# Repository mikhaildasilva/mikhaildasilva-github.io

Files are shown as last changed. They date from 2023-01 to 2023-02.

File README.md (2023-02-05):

## Cordelia 

---

<div align="center">
swimming
</div>
<div align="center"> <b>Video 1</b>: Ocillation gait</div><br>

## Design and Fabrication

---

<div align="center">
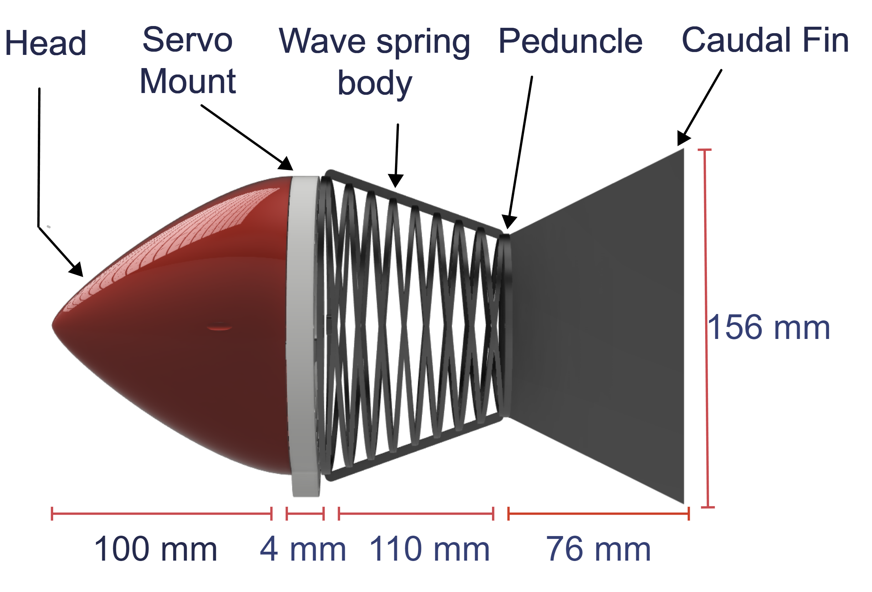
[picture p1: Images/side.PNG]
Parts

</div>

<div align="center"> <b>Figure 1</b>: Components of a single module fish </div><br>

<details open>
    <summary><b>Table 1</b>: Component and material used.</summary>
    <ol>
        <li>Component link takes you to <a href="https://gitlab.com/mikhaildasilva/fish/-/tree/main/CAD">CAD</a></li>
        <li>Material link take you to <a href="https://gitlab.com/mikhaildasilva/fish/-/tree/main/Additive%20Manufacturing/Material-Profile">Material-Profile</a></li>
    </ol>
</details>

| [Rigid head](https://gitlab.com/mikhaildasilva/fish/-/tree/main/CAD/Head)  | [Servo mount](https://gitlab.com/mikhaildasilva/fish/-/tree/main/CAD/Servo-Mount) | [Flexible body](https://gitlab.com/mikhaildasilva/fish/-/tree/main/CAD/Body) | [Caudal fin](https://gitlab.com/mikhaildasilva/fish/-/tree/main/CAD/Caudal-Fin) |
| :---: | :---: | :---: |:---: |
|[CPE](https://gitlab.com/mikhaildasilva/fish/-/tree/main/Additive%20Manufacturing/Material-Profile/CPE) | [PETG](https://gitlab.com/mikhaildasilva/fish/-/tree/main/Additive%20Manufacturing/Material-Profile/PETG) |  [TPU-95A](https://gitlab.com/mikhaildasilva/fish/-/tree/main/Additive%20Manufacturing/Material-Profile/TPU) |[TPU-95A](https://gitlab.com/mikhaildasilva/fish/-/tree/main/Additive%20Manufacturing/Material-Profile/TPU) |

---

:exclamation: A modular approach gives us the latitude to perform eclectic locomotion gaits by increasing the number of modules. For instance, 1 module can only perform an oscillatory pattern. Whereas a multi-module (3 and above) displays an undulatory motion. 

## Tendon-driven actuation 

---

<details open>
<summary>Actuation mechanism</summary>
<div align="center">
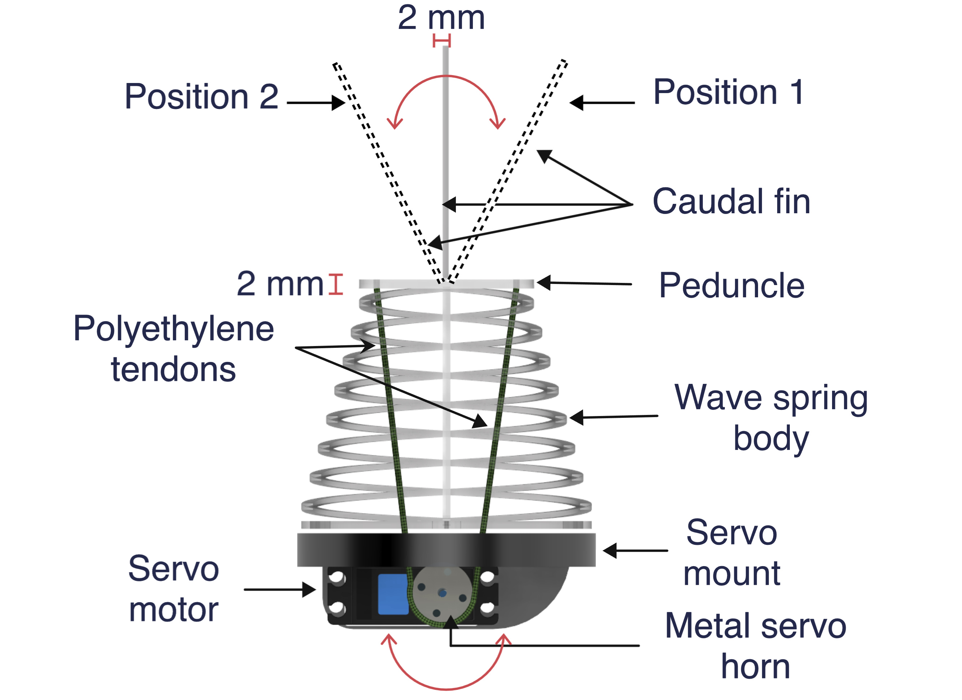
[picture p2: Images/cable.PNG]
Actuation
    
    </div>
</details>

<div align="center"> <b>Figure 2</b>: Cable spool mechanism. </div><br>

1. The tendon is wound around the servo while the servo motor is in its neutral position. 

2. When the servo motor is rotated in the clockwise direction the exercised tension on right hand side tendon bends the peduncle causing the caudal fin to move to position 1. Simultaneously a force is exerted on the other side of the line. 

3. Similarly when the servo motor moves in an anticlockwise direction the caudal fin moves to position  2.

<div align="center">
working
</div>
<div align="center"> <b>Video 2</b>: Cable spool mechanism in action</div><br>

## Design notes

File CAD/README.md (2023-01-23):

## CAD of Single Module Fish

---

The designs can be viewed in your browser with the help of Autodesk Viewer 

[Single Module Fish](https://autode.sk/3QX5BGi)

A pdf of the fish can be found a [document](https://gitlab.com/mikhaildasilva/fish/-/blob/main/CAD/fish1.pdf)

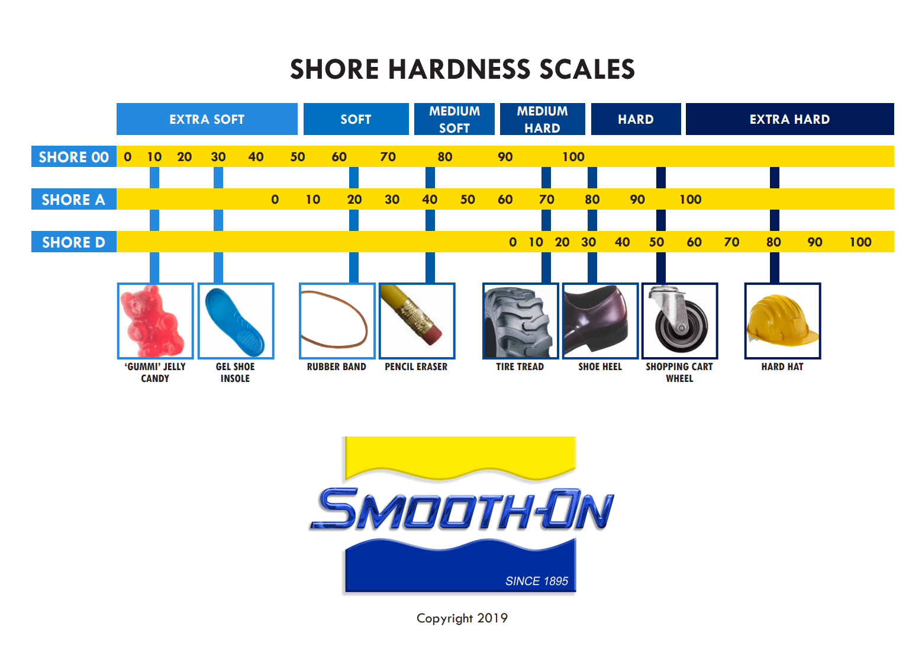
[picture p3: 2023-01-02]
Images/durometer_chart.PNG

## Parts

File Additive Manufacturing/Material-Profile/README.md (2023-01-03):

# Installation instructions

Refer to the [instruction document](https://gitlab.com/mikhaildasilva/fish/-/blob/main/Additive%20Manufacturing/Material-Profile/instructions.pdf)

YouTube [video](https://youtu.be/H2-ZPbIIFU8)

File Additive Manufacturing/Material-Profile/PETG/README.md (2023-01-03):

## CURA Material Profile for PETG 

--- 

### :warning: Polymaker PolyLite PETG 

- [Purchase link](https://us.polymaker.com/products/polylite-petg) from Polymaker store.

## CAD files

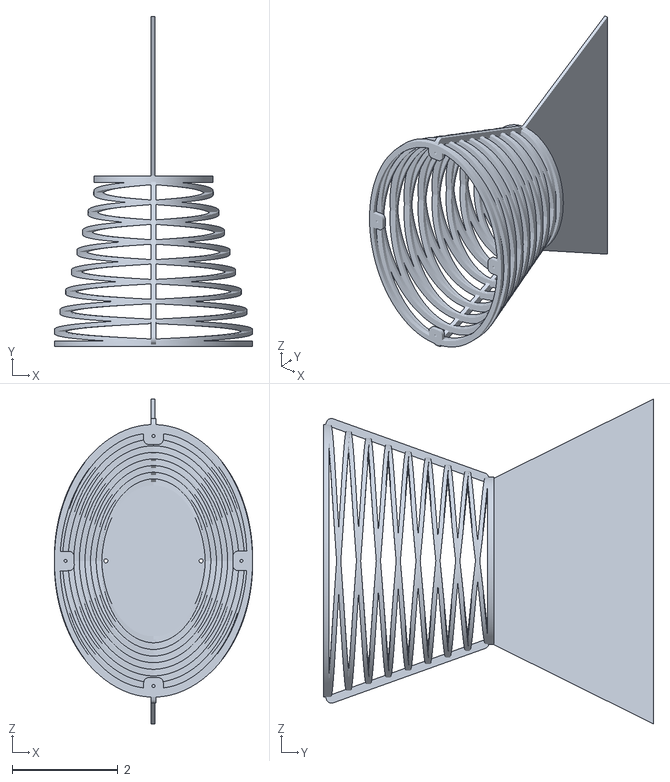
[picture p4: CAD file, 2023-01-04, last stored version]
CAD/Body/fish_end_segment.stl
3.75 x 6.24 x 6.14

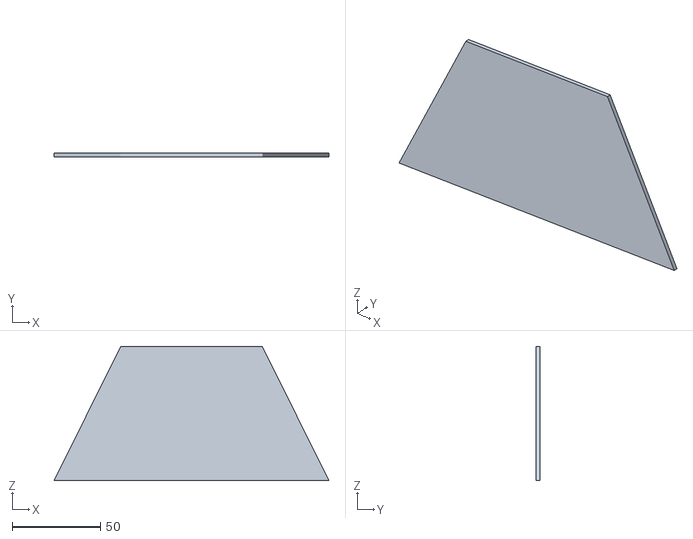
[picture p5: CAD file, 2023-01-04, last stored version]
CAD/Caudal-Fin/fin.stl
156.0 x 2.00 x 76.2

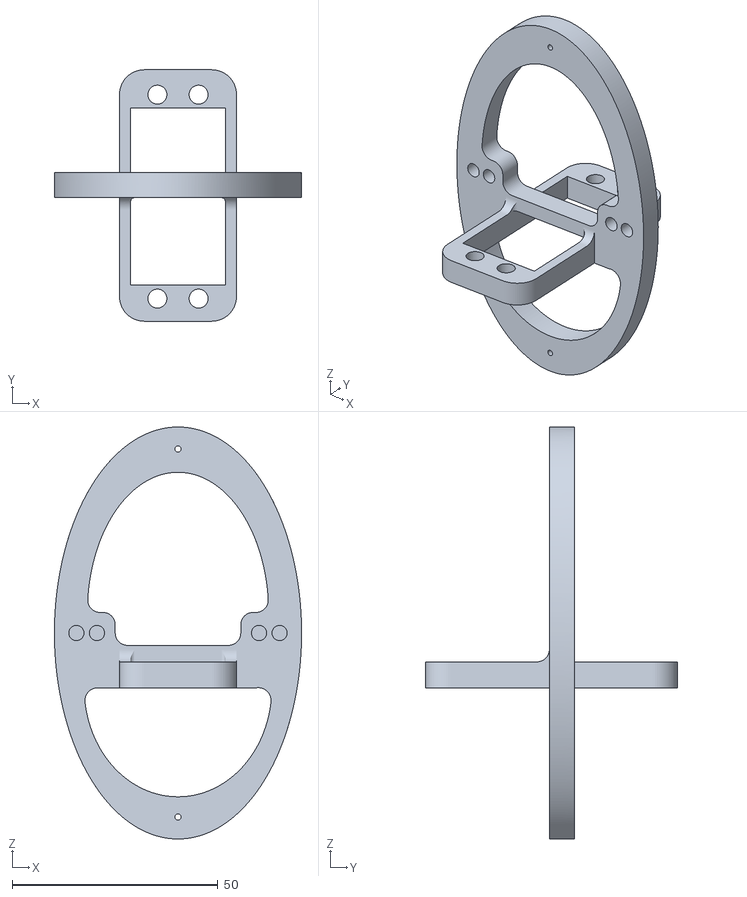
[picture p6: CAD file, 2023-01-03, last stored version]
CAD/Head/end_servo_support_bracket.stl
60.0 x 61.0 x 100.0

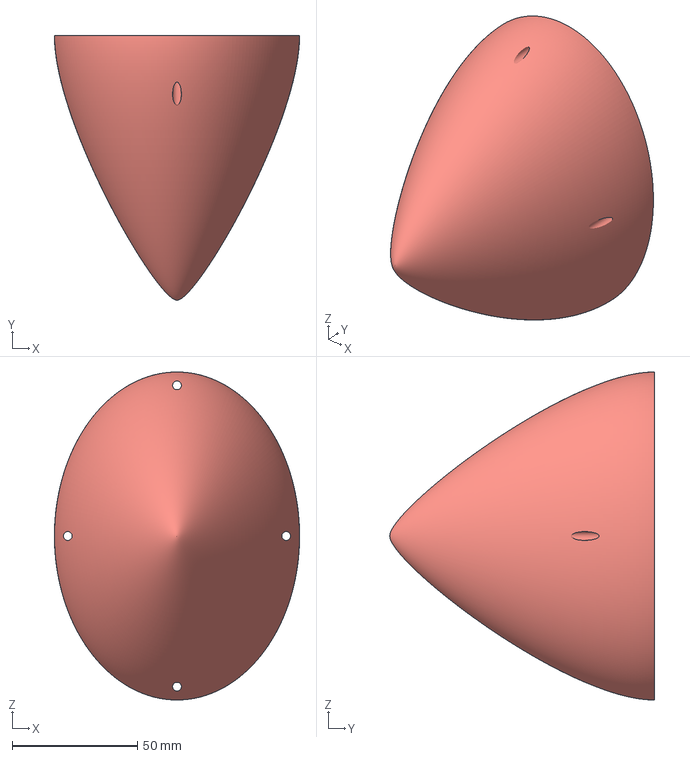
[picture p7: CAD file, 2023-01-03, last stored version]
CAD/Head/small_head_v6.3mf
97.8 x 105.5 x 130.8 mm

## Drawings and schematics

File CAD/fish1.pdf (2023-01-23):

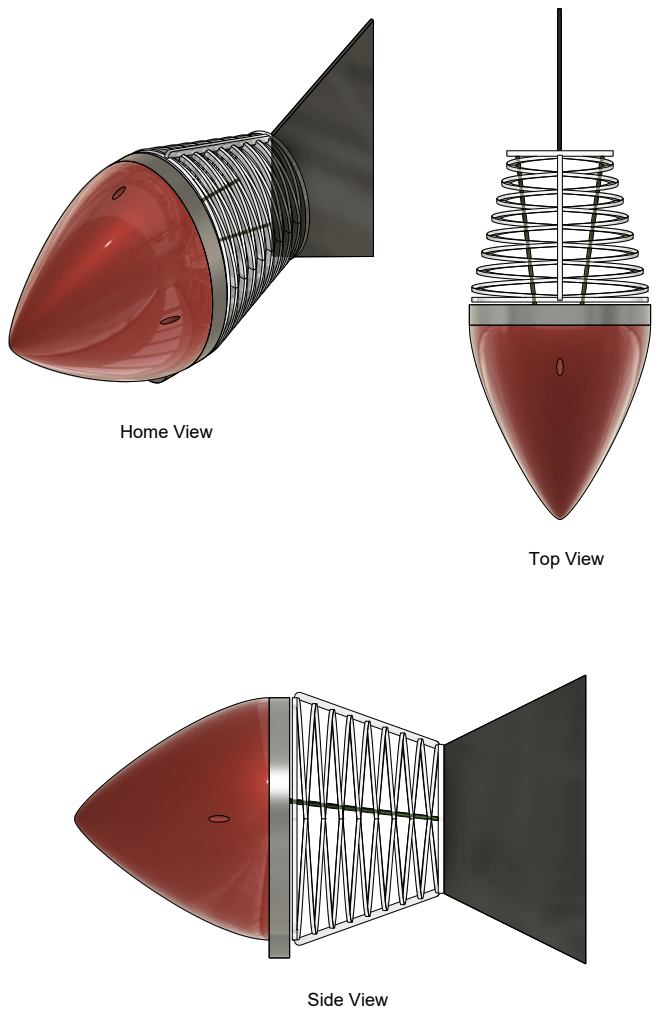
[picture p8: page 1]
Side View; Home View; Top View

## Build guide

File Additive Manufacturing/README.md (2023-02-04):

[[_TOC_]]
## Additive Manufacturing 

### What is Shore Hardness?

---

[Shore hardness](https://www.smooth-on.com/page/durometer-shore-hardness-scale/) scales provide a point of reference when measuring the ***hardness*** of materials. 

Shore Hardness chart<div align="center">Figure 1: *Shore Hardness chart that delineates hardness of ubiquitous items*</div>

### Why use Thermoplastic Polyurethane (TPU) instead of Silicone?

---

"Typical" soft robots utilise [Silicone](https://www.smooth-on.com/products/ecoflex-00-30/) of eclectic Shore Hardness' to impart compliance. One of the critical requirements in this project was the speed of prototyping. This is where Additive Manufacturing (3D Printing) using TPU excels. TPU offers elasticity and flexibility whilst maintaining robustness.  

#### A few challenges that arise when using Silicone:

- Silicone takes a considerable amount of time to cure ([4](https://www.smooth-on.com/products/ecoflex-00-30/) hours - [16](https://www.smooth-on.com/products/dragon-skin-30/) hours). 
- Necessity of additional expensive equipment
    - Vacuum chamber and pump to remove air bubbles.
    - Inverse moulds of the end product are required to pour Silicone in them.
    - Weighing scales, gloves, eye protection gear, an apron and non-lather soap are necessary. 
- Accurate mixing ratio of Part A and Part B followed by slow stirring of the liquid rubber.
- A release agent spray for "easy" removal of the part from the mould.

### 3D Printing using TPU filament

---

#### Hardware requirements 

1. Use a **Direct drive extruder** (DDE): 
    - TPU filaments with a shore hardness in the range of **75A-85A** are physically like rubber bands in layman's terms. 
    - By using a DDE, one is guiding the filament straight down into the nozzle.
    - _Caveat_: TPU **95A** is flexible yet rigid enough to be used by an FFF printer (Ultimaker S5) with a **Bowden tube extruder**. 
    - [Direct drive v/s Bowden tube](https://www.3djake.com/info/guide/direct-drive-extruder-vs-bowden-extruder) 
2. TPU is **hygroscopic**:
    - TPU needs to be dry to obtain [successful prints](https://www.printables.com/model/339968-wet-filament-in-comparison-to-dry-filament-tpu-fle). 
    - Store filament in a Mylar bag filled with silica. 
    - Invest or make a [filament drying box](https://www.amazon.com/SUNLU-Filament-Filadryer-Compatible-Filaments/dp/B0B4WKQR24)

#### Slicer Settings 

|Parameter |Value |Advice | 
|:---: |:---: |:--- |
|Print speed $(mm/sec)$ | $15 - 25$ |The slower the better. Unless you have a [Hemera](https://e3d-online.com/pages/hemera-feature-page)|
|Flow rate (%) | $106 - 110$ |Incrementally adjust based on quality of print.|
|Infill (%) | $10 - 15$ |Adjust based flexibility of final product.|
|Infill Pattern | Gyroid / Cross 3D |If final product needs to be **flexible**.|
|Infill Pattern | Cubic Subdivision / Grid |If final product needs to be **rigid**.|
|Retraction distance ($mm$) | 8 |Lower the retraction distance if filament is getting stuck within the gears (75A is prone to this problem.)|

### Vendor list TPU (as of 2 Jan. 2022)

--- 

:heavy_check_mark: = Easy to print. Can use the material profile from this repo as a boilerplate. 

:warning: = Difficult to print

|Difficulty | Filament Name  | Shore Hardness | 
|:---: | :---: | :---: |
| :heavy_check_mark: | [NinjaFlex](https://ninjatek.com/shop/ninjaflex/) | 85A | 
| :heavy_check_mark: | [Ultimaker-TPU](https://www.matterhackers.com/store/l/ultimaker-tpu-filament/sk/M5ZFDTT3) | 95A | 
| :warning:| [Chinchilla](https://ninjatek.com/shop/chinchilla/) | 75A |

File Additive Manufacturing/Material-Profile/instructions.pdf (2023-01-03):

## Step 1

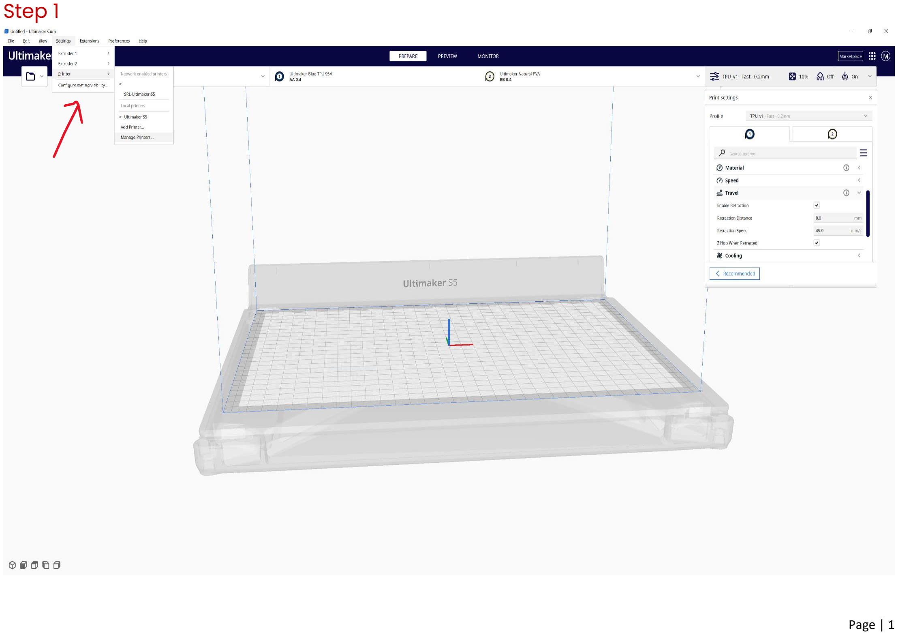
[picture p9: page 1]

Page | 1

## Step 2

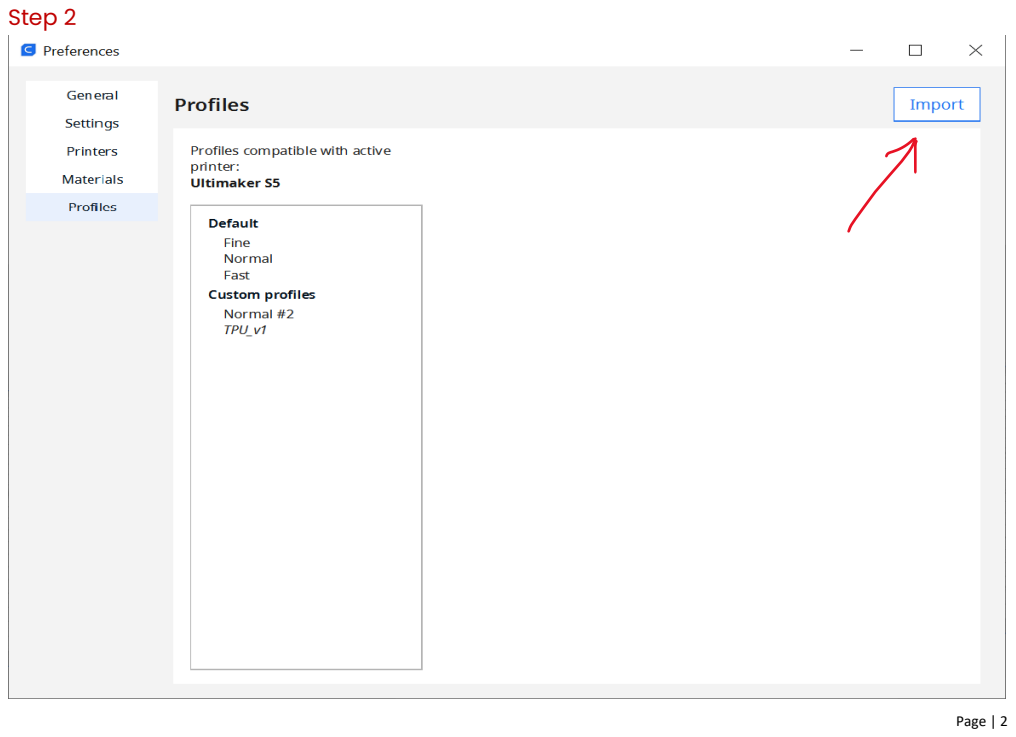
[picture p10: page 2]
Page | 2

Page | 3

## Step 3

Select the requisite profiles from ~/Downloads

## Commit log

2023-01-03 Upload New File
    [small_head_v6.3mf]
2023-01-23 Update 8 files
    - /CAD/Servo-Mount/.gitkeep
    - /CAD/Servo-Mount/end_servo_support_bracket.stl
    - /CAD/Head/.gitkeep
    - /CAD/Head/head_v6.stl
    - /CAD/Caudal-Fin/.gitkeep
    - /CAD/Caudal-Fin/fin.stl
    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
    [end_servo_support_bracket.stl, fin.stl, fish_end_segment.stl]
